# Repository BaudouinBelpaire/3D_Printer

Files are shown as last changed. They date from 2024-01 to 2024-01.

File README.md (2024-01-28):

# DIY CoreXY 3D Printer

During this project, I designed and assembled a homemade 3D printer based on a CoreXY architecture. This one has been designed on AutoDesk Fusion 360, and is made from 3D printed and laser cutted parts. The machine has a maxiumum printing volume of 200x200x200mm which is sufficient for regular prints.

## Specifications:
- The printing head is mounted on a CoreXY gantry enabling higher speeds and reducing the moving mass.
- The cubic frame makes the global architecture stiff which improves the print quality by absorbing the vibrations.
- The printer is running on an Arduino Mega2560 programmed with Marlin software.

## Mechanical design: 
The entire machine was designed on Fusion 360, and each part was either designed to be 3D printed/laser-cutted or bought online from suppliers. The CAD files from existing parts were found online on [GrabCAD](https://grabcad.com/library). The printer's assembly is shown in the next video:

https://github.com/BaudouinBelpaire/3D_Printer/assets/157626337/6a2e77a8-c60f-4968-856b-16abbe63af29

## Bill Of Materials:
Once the machine designed and simulated on Fusion 360, a [BOM](https://github.com/BaudouinBelpaire/3D_Printer/blob/main/BOM.xlsx) was established to realise the entire assembly. The parts were bought from different suppliers, and the MDF was purchased at Leroy Merlin to manufacture the panels and few other parts.

BOM

## Electronics:
The electronics ensure the actuation of the stepper motors according to the sequence of coordinates required to make the part. This one is composed of the 3 stepper motors for the XYZ directions and an additional one for the filament extrusion. The motors are controlled by motor drivers converting the digital pulses into electrical signals rotating the shaft. The calibration of the printer is ensured by mechanical endstops to know the initial position location. Finally, the extrusion and bed temperature are satisfied by a closed-loop system composed of a thermal sensor and heater. Each subsystem is controlled by the Arduino microprocessor which controls the actuators and receives feedbacks from the sensors. The circuit wiring is shown below: 

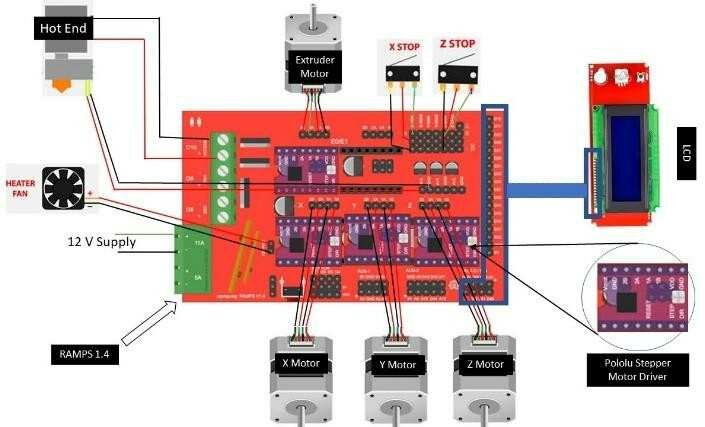
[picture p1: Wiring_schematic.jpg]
Wiring schematic


## Marlin software:
The Arduino board was programmed with the Marlin software which is a well-developed software for 3D printers. This one was adapted to the printer's parameters and flashed on the board.

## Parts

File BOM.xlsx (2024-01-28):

Subsystem | Item | Quantity | Price (€) | Link
Electronics | Stepper motors NEMA 17 (40N.cm) | 3 | 31 | https://www.banggood.com/fr/SIMAX3D-NEMA-17-Stepper-Motor-with-1m-Cable-for-3D-Printer-p-1661906.html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
 | Arduino Mega 2560 | 1 | 6.62 | https://www.banggood.com/fr/Mega2560-R3-ATMEGA2560-16-+-CH340-Module-Development-Board-Geekcreit-for-Arduino-products-that-work-with-official-Arduino-boards-p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
 | Ramps 1.4 | 1 | 9 | https://www.amazon.fr/DollaTek-Contr%C3%B4leur-dimprimante-Shield-Arduino/dp/B07DK429C5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
 | Mechanical endstops | 3 | 4.14 | https://fr.banggood.com/3pcs-RobotDyn-Opto-Coupler-Optical-End-stop-Module-Endstop-Switch-for-3D-Printer-and-CNC-Machine-Device-p-1619697.html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
 | A4988 motor driver | 4 | 10 | https://www.amazon.fr/A4988-Stepstick-Stepper-Dissipateur-chaleur-imprimante/dp/B0793K9KF8
 | Power supply 12V 30A | 1 | 15.67 | https://www.banggood.com/fr/12V-30A-360W-or-400W-Power-Supply-Adapter-for-ISDT-Q6-Pro-Toolkitrc-M8-Charger-p-1434238.html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
 | Plug power supply | 1 | 1.67 | https://www.banggood.com/fr/220V-or-110V-5A-Power-Outlet-Socket-With-Switch-And-6A-Fuse-For-3D-Printer-p-1149102.html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
 | Heat bed MK2B 12V-24V 214x214mm | 1 | 7.84 | https://www.banggood.com/fr/214x214mm-12V24V-Dual-Power-MK2B-PCB-Heated-Bed-Hot-Bed-For-Prusa-3D-Printer-p-1356056.html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
 | LCD screen 12864 RepRap | 1 | 9.37 | https://fr.aliexpress.com/item/32979641149.html
Printing Head | Extruding kit + motor | 1 | 14.73 | https://www.banggood.com/fr/Forward-or-Reverse-Direction-Metal-Extruder-Kit-With-NEMA-17-Stepper-Motor-For-RepRap-Prusa-i3-p-1258653.html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
 | Thermistors 100kOhms | 1 | 2.58 | https://www.banggood.com/fr/10-Pcs-NTC-100k-or-100ohm-Match-MK2a-1-pencent-Thermistor-Temperature-Sensor-For-3D-Printer-p-932646.html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
 | J-Head hotend + heater | 1 | 7.45 | https://www.banggood.com/fr/1_75mm-0_4mm-Filament-Bowden-Extruder-J-head-Hotend-For-3D-Printer-Part-p-1397654.html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
 | BL Touch | 1 | 8.74 | https://fr.aliexpress.com/item/1005004501631131.html
Mechanical | Motor support | 1 | 3.26 | https://www.banggood.com/fr/42MM-NEMA17-Stepper-Motor-Alloy-Steel-Mounting-Bracket-With-5x5x5cm-Screws-For-3D-Printer-p-1283233.html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
 | Coupler 8mm to 5mm | 1 | 2.47 | https://www.banggood.com/fr/2pcs-5mm-x-8mm-Aluminum-Flexible-Shaft-Coupling-OD19mm-x-L25mm-CNC-Stepper-Motor-Coupler-Connector-p-1507422.html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
 | Lead screw 8mm, 300mm + nut | 1 | 8.39 | https://fr.aliexpress.com/item/32819787167.html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
 | Idler pulleys | 8 | 4.04 | https://fr.aliexpress.com/item/32971394035.html
 | Rod 12mm, 300mm | 2 | 15 | https://fr.aliexpress.com/item/32332798910.html
 | Linear guide LMK12UU | 2 | 10.15 | https://fr.aliexpress.com/item/1005001639737687.html
 | Linear Guide MGN12 | 3 | 45.6 | https://www.banggood.com/fr/Machifit-MGN12-100-1000mm-Linear-Rail-Guide-with-MGN12H-Linear-Sliding-Guide-Block-CNC-Parts-p-1156260.html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
Material | MDF 6mm 80*60mm | 3 | 24.9 | https://www.leroymerlin.fr/produits/menuiserie/panneau-planche-et-materiaux-bois/panneau-bois-agglomere-mdf/panneau-bois-predecoupe/predecoupe-medium-mdf-natu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
TOTAL |  |  | 242.62

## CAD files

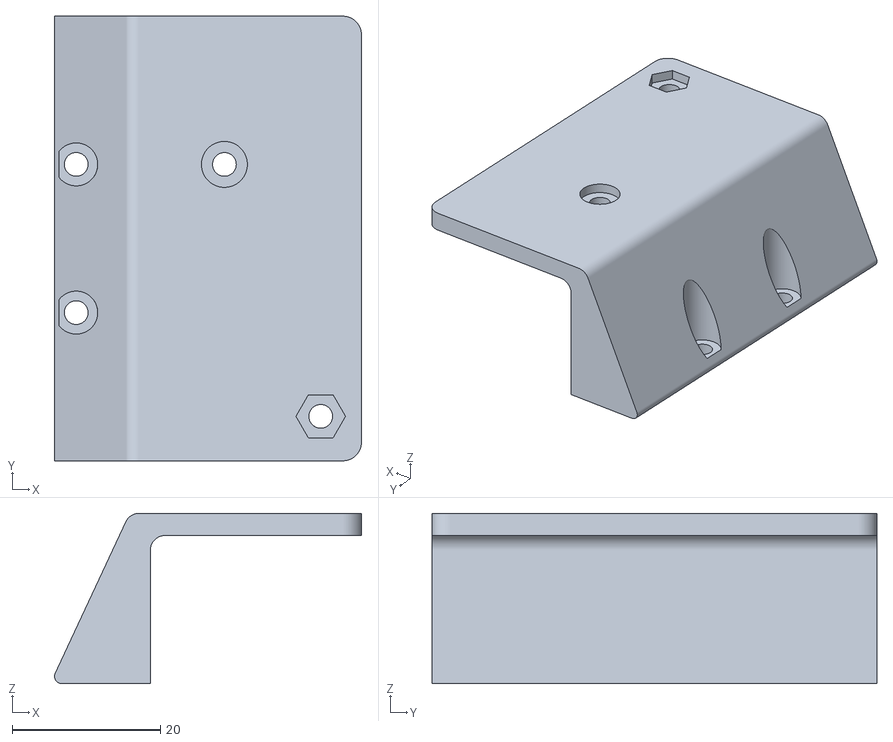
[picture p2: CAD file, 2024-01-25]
3D_printing/CoreXY_support.stl
41.4 x 60.0 x 23.0

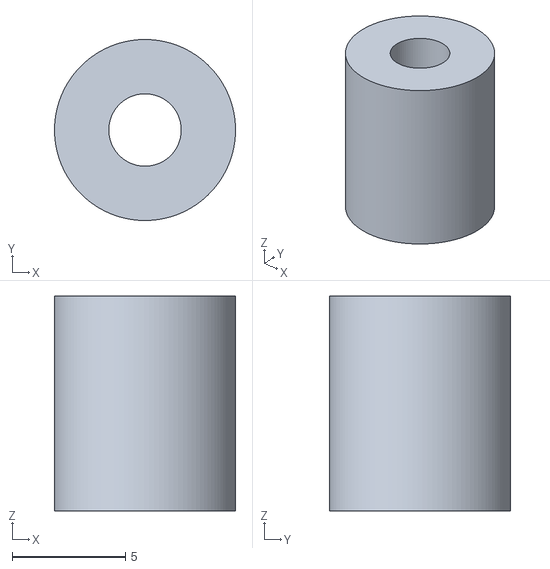
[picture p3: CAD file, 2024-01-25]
3D_printing/Files/Pulley_spacer.stl
8.00 x 8.00 x 9.50

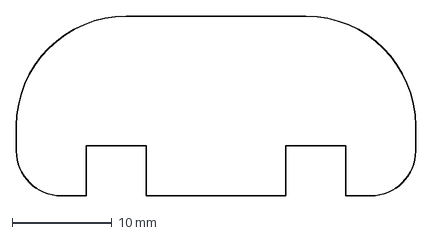
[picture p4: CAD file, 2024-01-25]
Laser_cutting/Files/Spool_support_semi-circle.dxf
40.0 x 18.0 mm

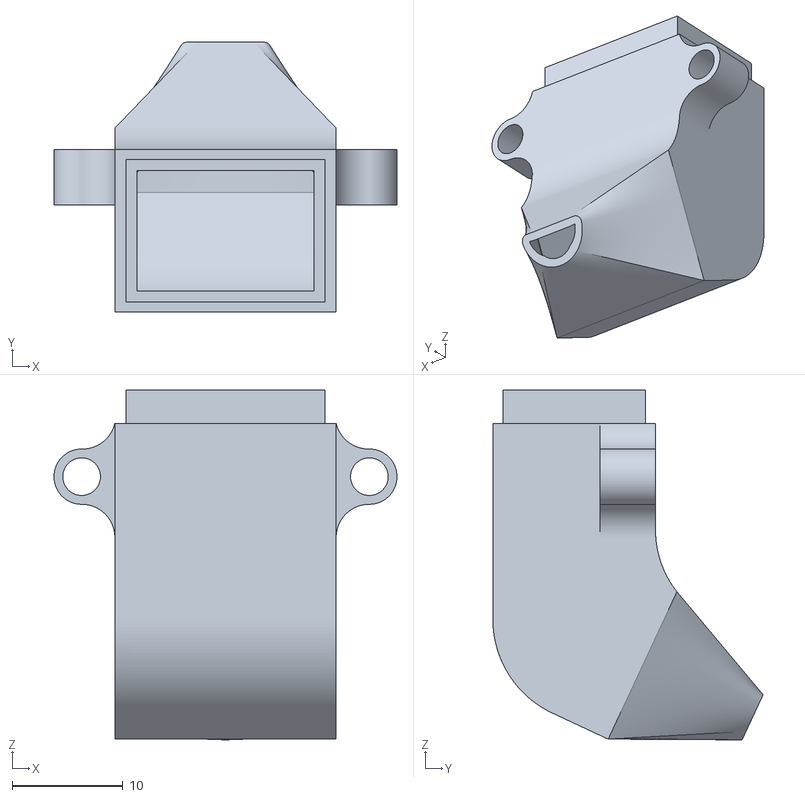
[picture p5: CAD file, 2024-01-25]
3D_printing/Fan_duct.stl
31.0 x 24.4 x 31.6

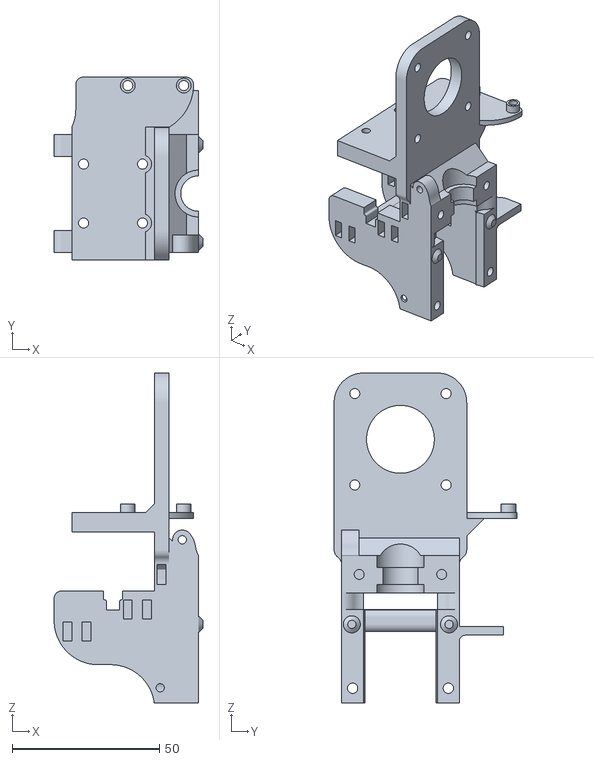
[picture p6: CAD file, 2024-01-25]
3D_printing/Files/Hotend_A.stl
50.5 x 62.0 x 112.0

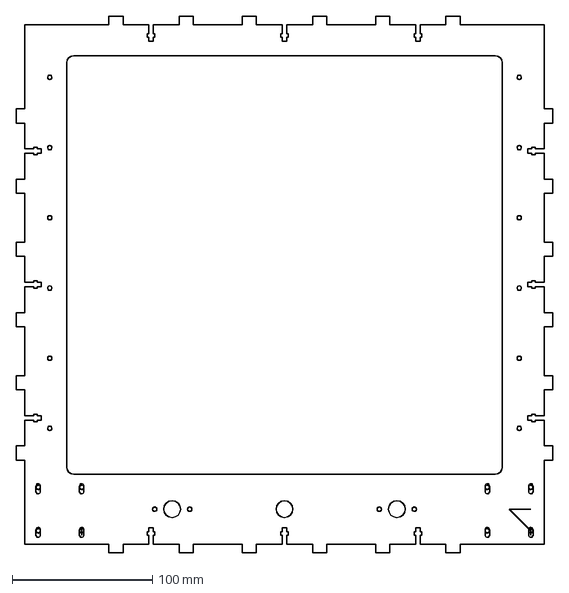
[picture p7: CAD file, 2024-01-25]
Laser_cutting/Files/Top_panel.dxf
382.0 x 382.0 mm

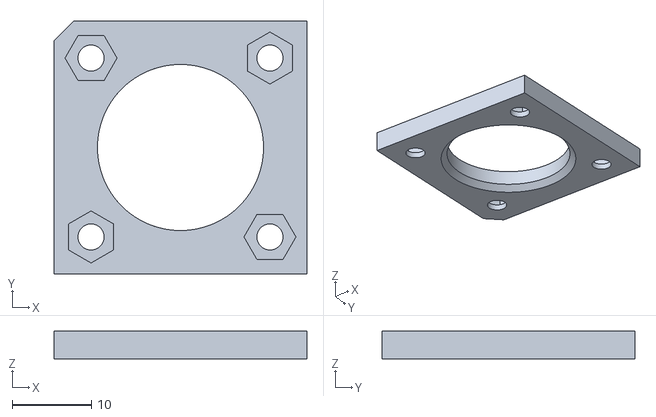
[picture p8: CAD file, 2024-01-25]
3D_printing/Centering_bed.stl
32.0 x 32.0 x 3.50

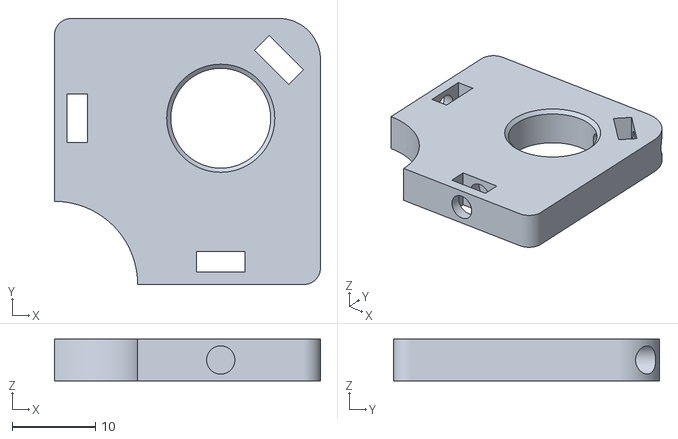
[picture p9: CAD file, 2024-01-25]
3D_printing/Files/Rod_holder_corner.stl
32.0 x 32.0 x 5.00

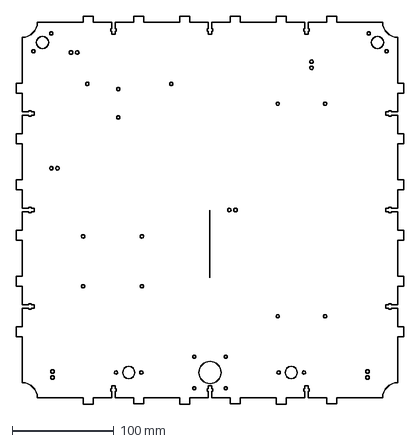
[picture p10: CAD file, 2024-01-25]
Laser_cutting/Files/Bottom_panel.dxf
382.0 x 382.0 mm

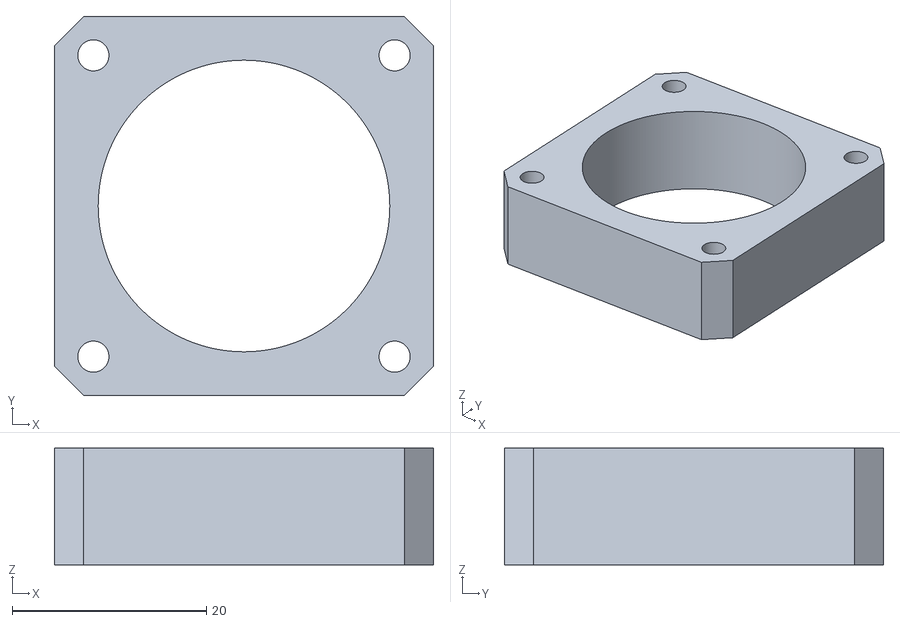
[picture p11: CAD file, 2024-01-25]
3D_printing/Files/Spacer_motor_12mm.stl
39.0 x 39.0 x 12.0

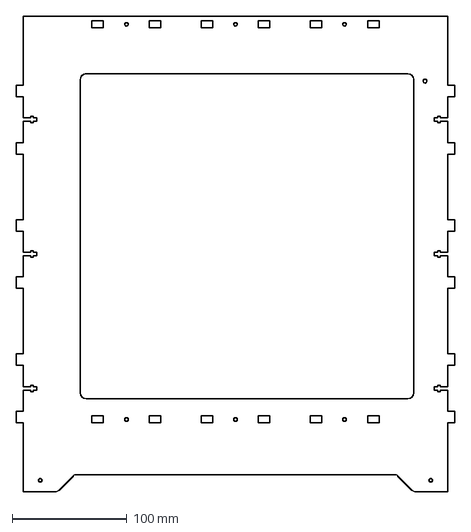
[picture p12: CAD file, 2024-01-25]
Laser_cutting/Files/Left_panel.dxf
382.0 x 414.0 mm

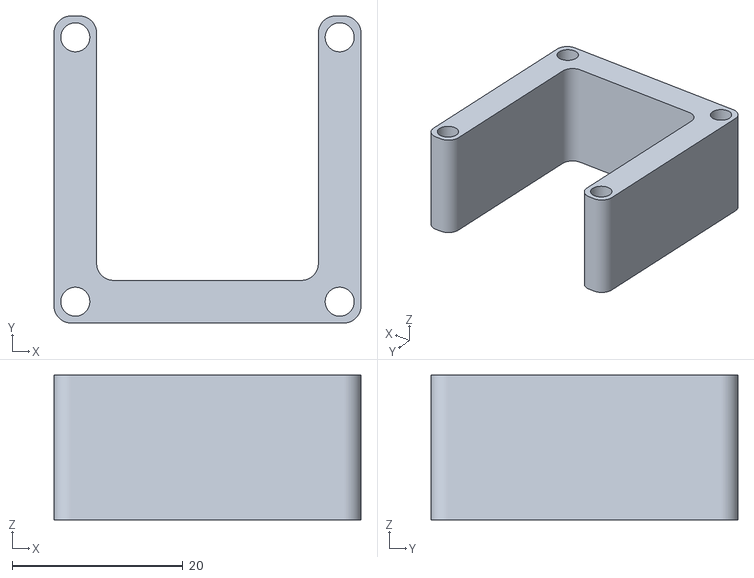
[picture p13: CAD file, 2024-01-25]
3D_printing/Files/Spacer_motor_17mm.stl
36.0 x 36.0 x 17.0

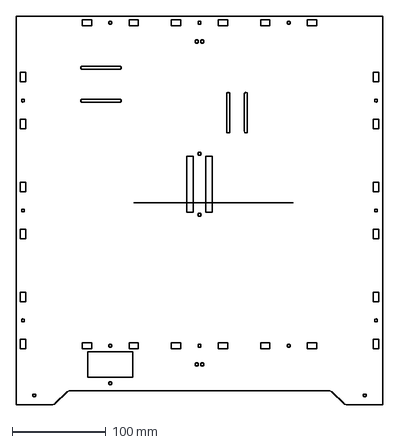
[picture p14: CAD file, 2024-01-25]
Laser_cutting/Files/Back_panel.dxf
390.0 x 414.0 mm

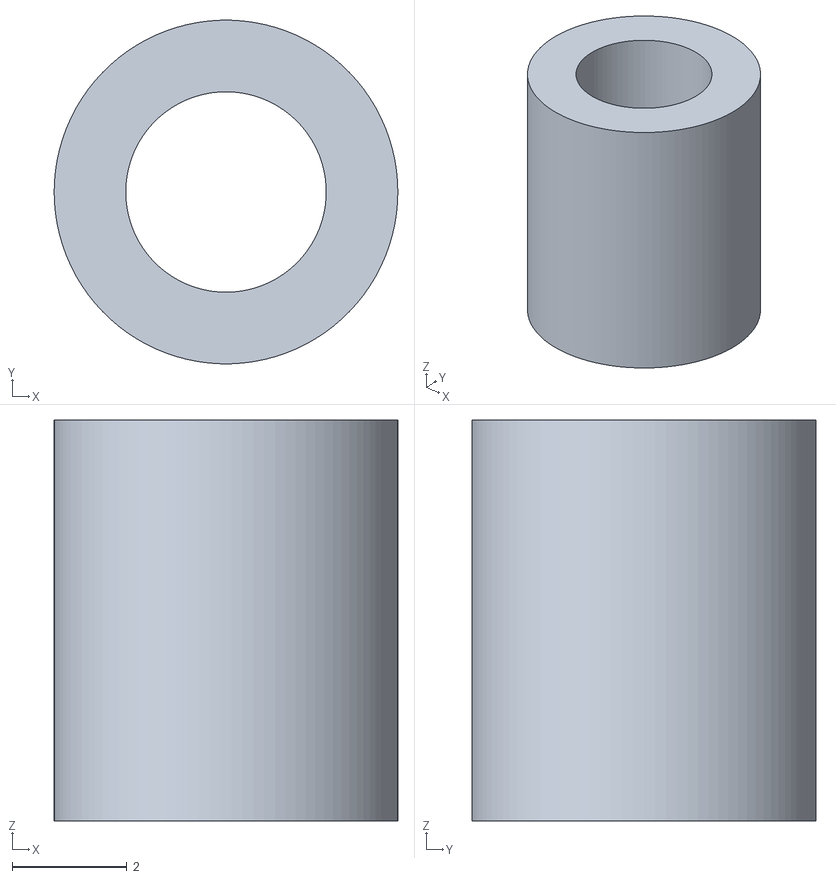
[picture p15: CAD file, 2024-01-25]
3D_printing/Files/Spacer_7mm.stl
6.00 x 6.00 x 7.00

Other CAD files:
Laser_cutting/Files/Front_panel.dxf
3D_printing/Files/Hotend_B.stl
Laser_cutting/Files/Spool_support_triangle.dxf
3D_printing/Files/LCD_screen_support.stl
3D_printing/Files/Motor_spacer_3mm.stl
3D_printing/Files/Pulley_holder.stl
3D_printing/Files/lcd_creen_supp.stl
3D_printing/Hotend_B.stl
3D_printing/LCD_screen_support.stl
3D_printing/Motor_spacer_3mm.stl
3D_printing/Pulley_holder.stl
3D_printing/lcd_creen_supp.stl
Laser_cutting/Files/Bed_support.dxf
Laser_cutting/Files/CoreXY_slider_support.dxf
Laser_cutting/Files/Right_panel.dxf
Laser_cutting/Files/Spool_support_spacer.dxf
Laser_cutting/Files/Z_rod_holder.dxf

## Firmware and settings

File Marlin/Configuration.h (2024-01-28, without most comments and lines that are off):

#pragma once
#define CONFIGURATION_H_VERSION 02010200
#define STRING_CONFIG_H_AUTHOR "(none, default config)" // Who made the changes.
#define SHOW_BOOTSCREEN
  #define MOTHERBOARD BOARD_RAMPS_14_EFB
#define SERIAL_PORT 0
#define BAUDRATE 250000
#define CUSTOM_MACHINE_NAME "BaudBaud 2000"
#define X_DRIVER_TYPE  A4988
#define Y_DRIVER_TYPE  A4988
#define Z_DRIVER_TYPE  A4988
#define E0_DRIVER_TYPE A4988
#define EXTRUDERS 1
#define DEFAULT_NOMINAL_FILAMENT_DIA 1.75
#define TEMP_SENSOR_0 5
#define TEMP_SENSOR_1 0
#define TEMP_SENSOR_2 0
#define TEMP_SENSOR_3 0
#define TEMP_SENSOR_4 0
#define TEMP_SENSOR_5 0
#define TEMP_SENSOR_6 0
#define TEMP_SENSOR_7 0
#define TEMP_SENSOR_BED 1
#define TEMP_SENSOR_PROBE 0
#define TEMP_SENSOR_CHAMBER 0
#define TEMP_SENSOR_COOLER 0
#define TEMP_SENSOR_BOARD 0
#define TEMP_SENSOR_REDUNDANT 0
#define DUMMY_THERMISTOR_998_VALUE  25
#define DUMMY_THERMISTOR_999_VALUE 100
#if TEMP_SENSOR_IS_MAX_TC(0)
  #define MAX31865_SENSOR_OHMS_0      100 // (Ω) Typically 100 or 1000 (PT100 or PT1000)
  #define MAX31865_CALIBRATION_OHMS_0 430 // (Ω) Typically 430 for Adafruit PT100; 4300 for Adafruit PT1000
#endif
#if TEMP_SENSOR_IS_MAX_TC(1)
  #define MAX31865_SENSOR_OHMS_1      100
  #define MAX31865_CALIBRATION_OHMS_1 430
#endif
#if TEMP_SENSOR_IS_MAX_TC(2)
  #define MAX31865_SENSOR_OHMS_2      100
  #define MAX31865_CALIBRATION_OHMS_2 430
#endif
#if HAS_E_TEMP_SENSOR
  #define TEMP_RESIDENCY_TIME         10  // (seconds) Time to wait for hotend to "settle" in M109
  #define TEMP_WINDOW                  1  // (°C) Temperature proximity for the "temperature reached" timer
  #define TEMP_HYSTERESIS              3  // (°C) Temperature proximity considered "close enough" to the target
#endif
#if TEMP_SENSOR_BED
  #define TEMP_BED_RESIDENCY_TIME     10  // (seconds) Time to wait for bed to "settle" in M190
  #define TEMP_BED_WINDOW              1  // (°C) Temperature proximity for the "temperature reached" timer
  #define TEMP_BED_HYSTERESIS          3  // (°C) Temperature proximity considered "close enough" to the target
#endif
#if TEMP_SENSOR_CHAMBER
  #define TEMP_CHAMBER_RESIDENCY_TIME 10  // (seconds) Time to wait for chamber to "settle" in M191
  #define TEMP_CHAMBER_WINDOW          1  // (°C) Temperature proximity for the "temperature reached" timer
  #define TEMP_CHAMBER_HYSTERESIS      3  // (°C) Temperature proximity considered "close enough" to the target
#endif
#if TEMP_SENSOR_REDUNDANT
  #define TEMP_SENSOR_REDUNDANT_SOURCE    E1  // The sensor that will provide the redundant reading.
  #define TEMP_SENSOR_REDUNDANT_TARGET    E0  // The sensor that we are providing a redundant reading for.
  #define TEMP_SENSOR_REDUNDANT_MAX_DIFF  10  // (°C) Temperature difference that will trigger a print abort.
#endif
#define HEATER_0_MINTEMP   5
#define HEATER_1_MINTEMP   5
#define HEATER_2_MINTEMP   5
#define HEATER_3_MINTEMP   5
#define HEATER_4_MINTEMP   5
#define HEATER_5_MINTEMP   5
#define HEATER_6_MINTEMP   5
#define HEATER_7_MINTEMP   5
#define BED_MINTEMP        5
#define CHAMBER_MINTEMP    5
#define HEATER_0_MAXTEMP 275
#define HEATER_1_MAXTEMP 275
#define HEATER_2_MAXTEMP 275
#define HEATER_3_MAXTEMP 275
#define HEATER_4_MAXTEMP 275
#define HEATER_5_MAXTEMP 275
#define HEATER_6_MAXTEMP 275
#define HEATER_7_MAXTEMP 275
#define BED_MAXTEMP      150
#define CHAMBER_MAXTEMP  60
#define HOTEND_OVERSHOOT 15   // (°C) Forbid temperatures over MAXTEMP - OVERSHOOT
#define BED_OVERSHOOT    10   // (°C) Forbid temperatures over MAXTEMP - OVERSHOOT
#define COOLER_OVERSHOOT  2   // (°C) Forbid temperatures closer than OVERSHOOT
#define PIDTEMP          // See the PID Tuning Guide at https://reprap.org/wiki/PID_Tuning
#define BANG_MAX 255     // Limits current to nozzle while in bang-bang mode; 255=full current
#define PID_MAX BANG_MAX // Limits current to nozzle while PID is active (see PID_FUNCTIONAL_RANGE below); 255=full current
#define PID_K1 0.95      // Smoothing factor within any PID loop
    #define DEFAULT_Kp  22.20
    #define DEFAULT_Ki   1.08
    #define DEFAULT_Kd 114.00
#define MAX_BED_POWER 255 // limits duty cycle to bed; 255=full current
#define MAX_CHAMBER_POWER 255 // limits duty cycle to chamber heater; 255=full current
  #define PID_FUNCTIONAL_RANGE 10 // If the temperature difference between the target temperature and the actual temperature
#define PREVENT_COLD_EXTRUSION
#define EXTRUDE_MINTEMP 170
#define PREVENT_LENGTHY_EXTRUDE
#define EXTRUDE_MAXLENGTH 200
#define THERMAL_PROTECTION_HOTENDS // Enable thermal protection for all extruders
#define THERMAL_PROTECTION_BED     // Enable thermal protection for the heated bed
#define THERMAL_PROTECTION_CHAMBER // Enable thermal protection for the heated chamber
#define THERMAL_PROTECTION_COOLER  // Enable thermal protection for the laser cooling
#define COREXY
#define USE_XMIN_PLUG
#define USE_ZMIN_PLUG
#define USE_YMAX_PLUG
#define ENDSTOPPULLUPS
#define X_MIN_ENDSTOP_INVERTING true // Set to true to invert the logic of the endstop.
#define Y_MIN_ENDSTOP_INVERTING true // Set to true to invert the logic of the endstop.
#define Z_MIN_ENDSTOP_INVERTING false // Set to true to invert the logic of the endstop.
#define I_MIN_ENDSTOP_INVERTING false // Set to true to invert the logic of the endstop.
#define J_MIN_ENDSTOP_INVERTING false // Set to true to invert the logic of the endstop.
#define K_MIN_ENDSTOP_INVERTING false // Set to true to invert the logic of the endstop.
#define U_MIN_ENDSTOP_INVERTING false // Set to true to invert the logic of the endstop.
#define V_MIN_ENDSTOP_INVERTING false // Set to true to invert the logic of the endstop.
#define W_MIN_ENDSTOP_INVERTING false // Set to true to invert the logic of the endstop.
#define X_MAX_ENDSTOP_INVERTING true // Set to true to invert the logic of the endstop.
#define Y_MAX_ENDSTOP_INVERTING true // Set to true to invert the logic of the endstop.
#define Z_MAX_ENDSTOP_INVERTING false // Set to true to invert the logic of the endstop.
#define I_MAX_ENDSTOP_INVERTING false // Set to true to invert the logic of the endstop.
#define J_MAX_ENDSTOP_INVERTING false // Set to true to invert the logic of the endstop.
#define K_MAX_ENDSTOP_INVERTING false // Set to true to invert the logic of the endstop.
#define U_MAX_ENDSTOP_INVERTING false // Set to true to invert the logic of the endstop.
#define V_MAX_ENDSTOP_INVERTING false // Set to true to invert the logic of the endstop.
#define W_MAX_ENDSTOP_INVERTING false // Set to true to invert the logic of the endstop.
#define Z_MIN_PROBE_ENDSTOP_INVERTING false // Set to true to invert the logic of the probe.
#define DEFAULT_AXIS_STEPS_PER_UNIT   { 80, 80, 1600, 92.65 }
#define DEFAULT_MAX_FEEDRATE          { 300, 300, 5, 25 }
#define DEFAULT_MAX_ACCELERATION      { 3000, 3000, 100, 10000 }
#define DEFAULT_ACCELERATION          3000    // X, Y, Z and E acceleration for printing moves
#define DEFAULT_RETRACT_ACCELERATION  3000    // E acceleration for retracts
#define DEFAULT_TRAVEL_ACCELERATION   3000    // X, Y, Z acceleration for travel (non printing) moves
#define DEFAULT_EJERK    5.0  // May be used by Linear Advance
  #define JUNCTION_DEVIATION_MM 0.013 // (mm) Distance from real junction edge
  #define JD_HANDLE_SMALL_SEGMENTS    // Use curvature estimation instead of just the junction angle
#define Z_MIN_PROBE_USES_Z_MIN_ENDSTOP_PIN
#define BLTOUCH
#define NOZZLE_TO_PROBE_OFFSET { -27.5, 0, -3 }
#define PROBING_MARGIN 10
#define XY_PROBE_FEEDRATE (133*60)
#define Z_PROBE_FEEDRATE_FAST (4*60)
#define Z_PROBE_FEEDRATE_SLOW (Z_PROBE_FEEDRATE_FAST / 2)
#define Z_CLEARANCE_DEPLOY_PROBE   10 // Z Clearance for Deploy/Stow
#define Z_CLEARANCE_BETWEEN_PROBES  5 // Z Clearance between probe points
#define Z_CLEARANCE_MULTI_PROBE     5 // Z Clearance between multiple probes
#define Z_PROBE_LOW_POINT          -2 // Farthest distance below the trigger-point to go before stopping
#define Z_PROBE_OFFSET_RANGE_MIN -20
#define Z_PROBE_OFFSET_RANGE_MAX 20
#define X_ENABLE_ON 0
#define Y_ENABLE_ON 0
#define Z_ENABLE_ON 0
#define E_ENABLE_ON 0 // For all extruders
#define DISABLE_X false
#define DISABLE_Y false
#define DISABLE_Z false
#define DISABLE_E false             // Disable the extruder when not stepping
#define DISABLE_INACTIVE_EXTRUDER   // Keep only the active extruder enabled
#define INVERT_X_DIR false
#define INVERT_Y_DIR false
#define INVERT_Z_DIR false
#define INVERT_E0_DIR false
#define INVERT_E1_DIR false
#define INVERT_E2_DIR false
#define INVERT_E3_DIR false
#define INVERT_E4_DIR false
#define INVERT_E5_DIR false
#define INVERT_E6_DIR false
#define INVERT_E7_DIR false
#define X_HOME_DIR -1
#define Y_HOME_DIR 1
#define Z_HOME_DIR -1
#define X_BED_SIZE 200
#define Y_BED_SIZE 200
#define X_MIN_POS 0
#define Y_MIN_POS 0
#define Z_MIN_POS 0
#define X_MAX_POS X_BED_SIZE
#define Y_MAX_POS Y_BED_SIZE
#define Z_MAX_POS 200
#define MIN_SOFTWARE_ENDSTOPS
  #define MIN_SOFTWARE_ENDSTOP_X
  #define MIN_SOFTWARE_ENDSTOP_Y
  #define MIN_SOFTWARE_ENDSTOP_Z
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

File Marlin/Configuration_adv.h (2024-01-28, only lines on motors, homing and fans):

#define E0_AUTO_FAN_PIN -1
#define E1_AUTO_FAN_PIN -1
#define E2_AUTO_FAN_PIN -1
#define E3_AUTO_FAN_PIN -1
#define E4_AUTO_FAN_PIN -1
#define E5_AUTO_FAN_PIN -1
#define E6_AUTO_FAN_PIN -1
#define E7_AUTO_FAN_PIN -1
#define CHAMBER_AUTO_FAN_PIN -1
#define COOLER_AUTO_FAN_PIN -1
#define HOMING_BUMP_MM      { 5, 5, 2 }       // (linear=mm, rotational=°) Backoff from endstops after first bump
#define HOMING_BUMP_DIVISOR { 2, 2, 4 }       // Re-Bump Speed Divisor (Divides the Homing Feedrate)
#define MICROSTEP_MODES { 16, 16, 16, 16, 16, 16 } // [1,2,4,8,16]

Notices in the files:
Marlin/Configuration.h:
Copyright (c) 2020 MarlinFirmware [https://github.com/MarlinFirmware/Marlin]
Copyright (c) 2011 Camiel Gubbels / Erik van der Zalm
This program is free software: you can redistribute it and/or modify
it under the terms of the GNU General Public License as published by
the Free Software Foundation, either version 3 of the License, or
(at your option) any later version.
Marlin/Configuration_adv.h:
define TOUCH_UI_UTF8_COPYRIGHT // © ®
